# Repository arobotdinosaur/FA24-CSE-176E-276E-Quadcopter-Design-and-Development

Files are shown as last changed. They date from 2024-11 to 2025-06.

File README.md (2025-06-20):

Raw Quadcopters
Quadcopters designed by Kaustubh Kanagalekar and Alexander Haken

## Introduction

In this project class, we were challenged to design a printed circuit board (PCB) quadcopter and program it using Arduino software in order to achieve flight. 

The class was broken into multiple smaller milestones- PCB design for electronic components, PCB design for quadcopter, sensor filtering and calibration, Proportional, Integral, Derivative (PID) tuning, PCB quadcopter assembly, and flight. As we were designing the PCB quadcopter using computer software, we were provided with a test flight control board (FCB) that we could work on concurrently. We could use either the FCB or the custom PCB quadcopter for demonstration purposes. 

The skills that we learned from the class were-
1. PCB design and fabrication
2. Embedded systems programming 
3. Control theory and sensor calibration 

## Electronic Design

Using Fusion 360, we were tasked with designing the following components from scratch- 

1. Resistor (0805 0Ohm) 
2. Red LED 
3. MOSFET (N-channel) 
4. Inertial measurement unit (IMU) (LSM6DSOXTR 6-Axis) 

We referenced the data sheets for each component online and extensively studied the footprints. 
More specifically, we utilised the footprints tab in Fusion 360 to add SMD pads, silkscreens, keepouts, etc. to accurately replicate the dimensions. 

We also took advantage of the automated building tool at times to accurately build the electronic components.  

Footprint of the resistor
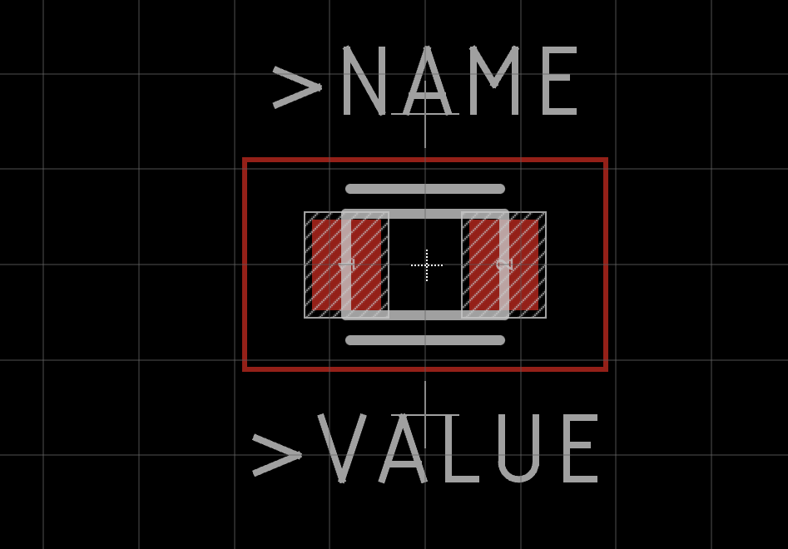
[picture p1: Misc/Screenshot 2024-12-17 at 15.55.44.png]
Footprint of the resistor
 

Footprint of the LED 
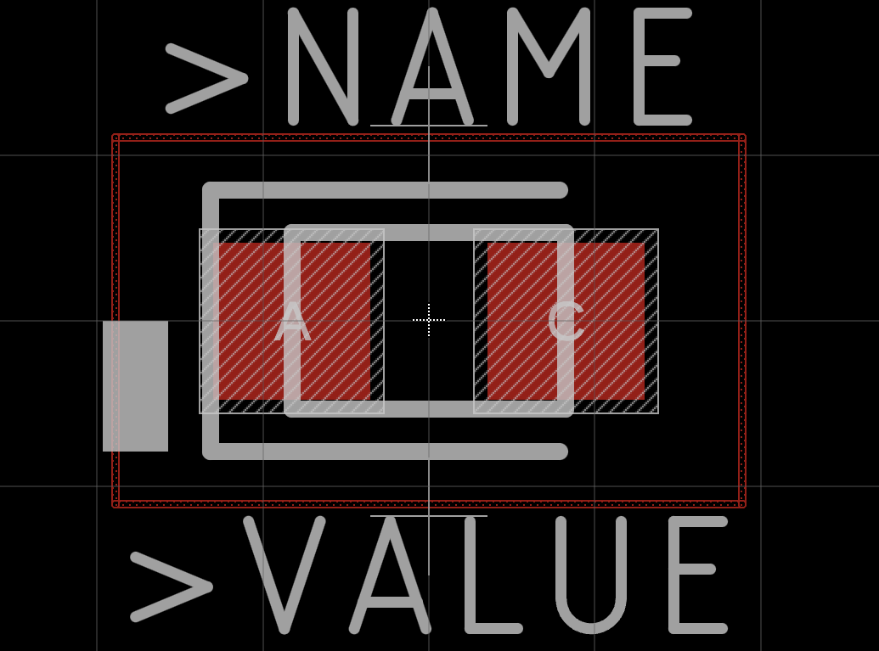
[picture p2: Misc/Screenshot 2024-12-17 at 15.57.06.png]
Footprint of the LED


Footprint of the MOSFET 
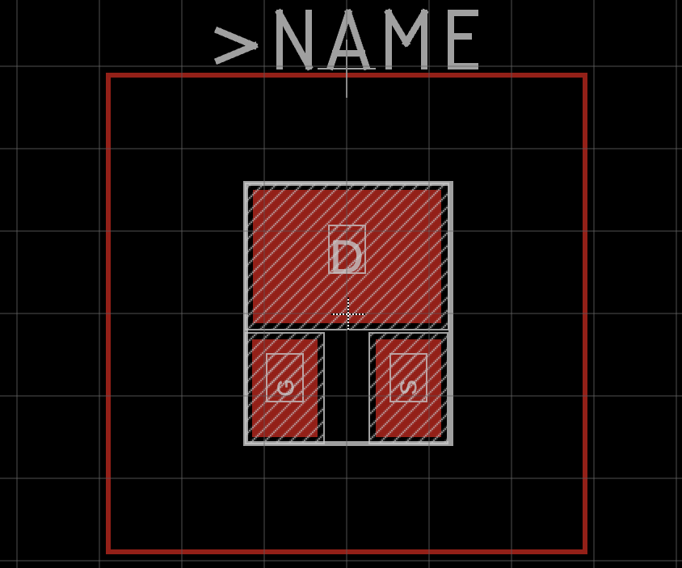
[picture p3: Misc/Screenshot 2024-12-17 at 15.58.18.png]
MOSFET Footprint
 

Footprint of the IMU 
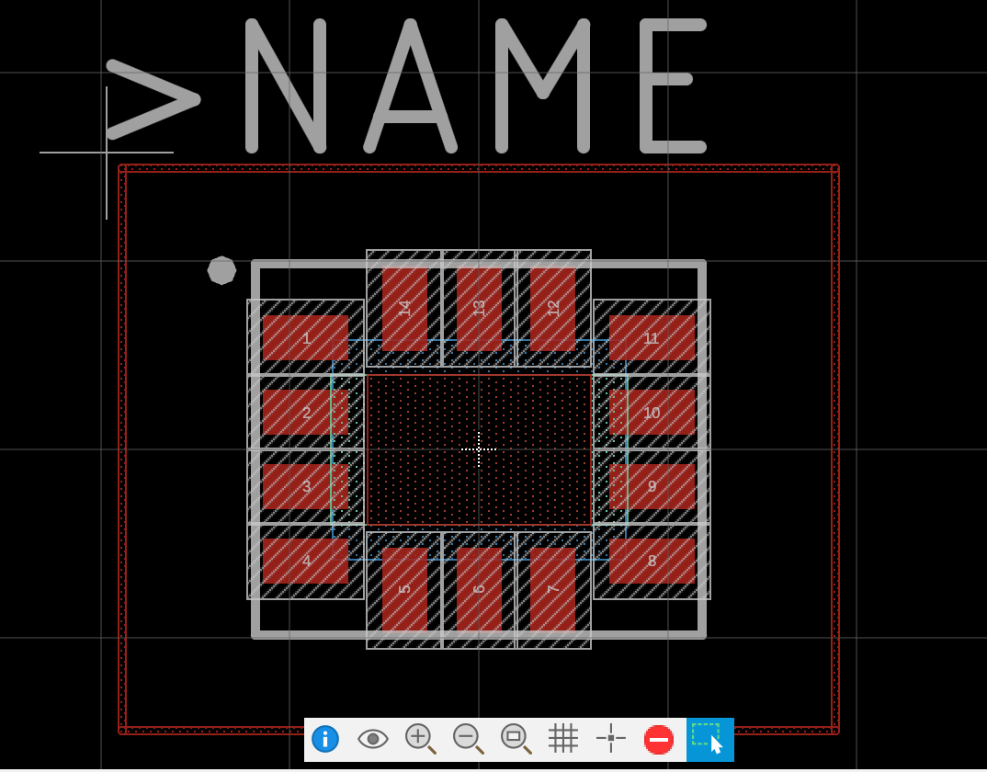
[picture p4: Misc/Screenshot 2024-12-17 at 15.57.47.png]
IMU Footprint


After creating the footprints, we built symbols for each electronic component using the standard IEEE styling conventions using the symbols tab. 

Finally, we connected the footprints and the symbols of each component in the components tab so that we could use them in our quadcopter schematic and design. 

We ensured that we met all the necessary guidelines and requirements set forth by the PCB manufacturer and instructor in our designs.  

## Quadcopter Design 

We were tasked with creating the schematic for the PCB quadcopter. In addition to our custom made components, we were also provided with additional parts from the instructor. 
The quadcopter had multiple smaller sketches- 
1. The microcontroller connections  
2. Bootloader 
3. IMU 
4. Debug/Rescue Header 
5. Motor Driver 
6. Netbridge and power supply 

### Microcontroller connections
We connected various pins and components to the microcontroller. The most significant connection we had was the balun (used for allowing balanced and unbalanced lines to be interfaced without major disturbances in impedances). This was significant as it allowed us to securely connect the antenna in our design. We were deliberate in our antenna placement as incorrect placements would yield spotty data transmission, and the quadcopter may not be able to fly.  

### Bootloader 
The primary objective of including the bootloader was  to load code to the microcontroller. Pins were connected to the microcontroller from the bootloader. 

### IMU 
We established a communication protocol with the microcontroller using I2C (Inter-Integrated Circuit). We incorporated two wires (Serial Data Line and Serial Clock Line) to transmit data between the microcontroller and IMU. 

### Debug/Rescue Header 
The rescue header was incorporated in order to help with debugging signals during testing. We also added a IMU reuse header in case our soldered IMU had issues. 

### Motor Driver 
We built four copies of the motor driver sketch as there were four motors driving the quadcopter. We included motor pads, mosfets, and a diode in the sketch. More importantly, we also included a decoupling capacitor to help absorb switching noise from the motors.

### Netbridge and Power Supply 
We designed a low-dropout voltage regulator in the schematic to provide a stable power output of 3V to the motors. This was because the batteries were providing power ranging from 4V to 5V. We had two power rails: An unregulated power rail (called VBAT) that provides power to the motors and input of the voltage regulator and is driven directly by the battery, and a regulated supply driven by the voltage regulator (called 3V) 

A netbridge was also created in order to electrically connect two nets in a schematic while keeping the nets separate in schematic . This was done to connect digital ground (BAT_GND) to regular ground. 

Image of the overall schematic 
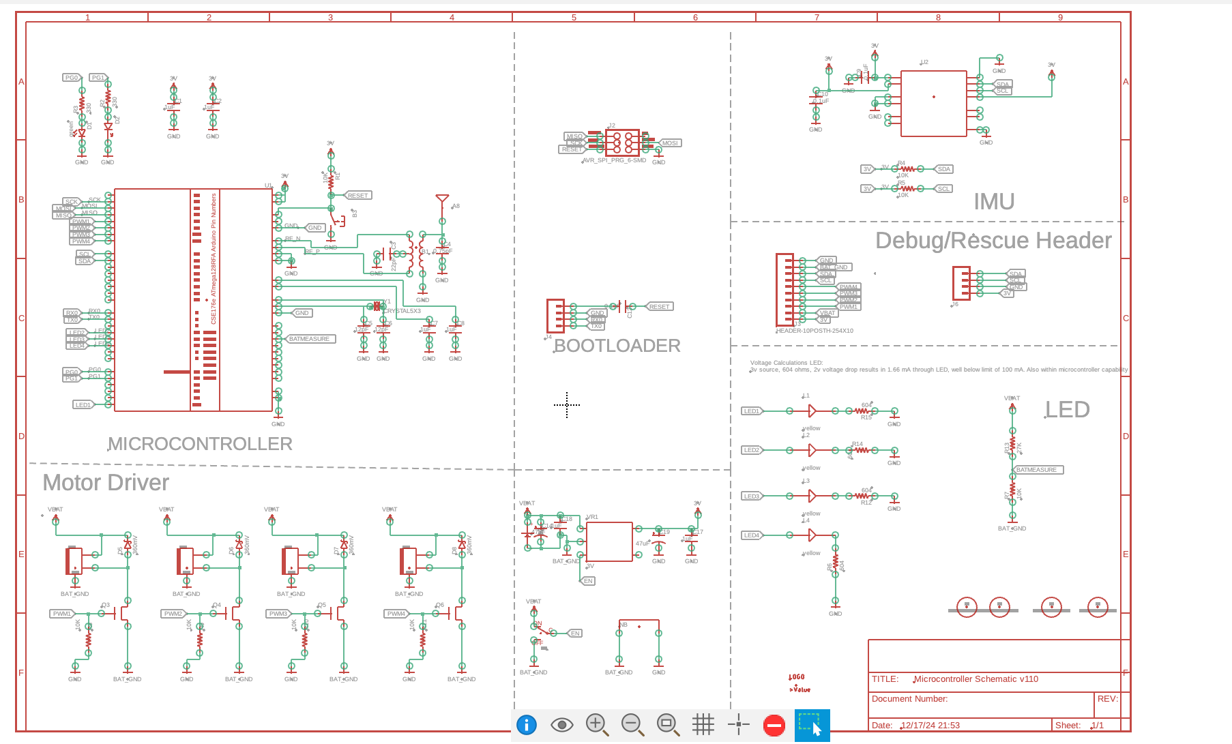
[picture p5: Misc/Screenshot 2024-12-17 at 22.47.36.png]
Schematic


### PCB Design 
We created a custom shape for the quadcopter and placed all the necessary components from the sketch to the board. The placement of some components were extremely important- for example, the antenna had to be placed near the edge of the board for uninterrupted communication, and the IMU had to be placed at the centre for accurate measurements. The crystal was placed close to the microcontroller, and the motor controllers were placed at the edges of the board. 

We primarily used the autorouter to route all wirings and connections, except in the case of the antenna and parts of the microcontroller. The antenna had to be connected with a large wire (50 mm) manually to the balun and other components (such as the corresponding  microcontroller pins and capacitors). The crystal also had to manually routed with specific pins of the microcontroller. We utilized differential pairs for sending the signals from the antenna and crystal back to the microcontroller due to the sensitivity of these components.

The board had to fit under a 13.9 cm square requirement  with motor holes of 12.2 mm for optimal placement. 
In Fusion 360, the board was aligned to a 1 mm grid for aesthetic reasons. 

We had four layers on the board in order to manage all the wirings and connections succinctly. We had a top layer, bottom layer, and two internal layers (one for 3V/VBAT and the other for GND/BAT_GND). The top and bottom layers involved signal routing for connecting various electronic components. The bottom plan was used whenever possible to reduce electrical noise. The 3V/VBAT and GND/BAT_GND layers were exclusively used for delivering power and ground signals, respectively. The traces that carried both power and ground signals were as short as possible to provide a low-resistance path for current to flow. 
We took care to leave a gap in all the layers beneath the IMU as the manufacture specified that we should not have metal underneath it for best performance.
 
Image of the connected boards in Fusion 360.
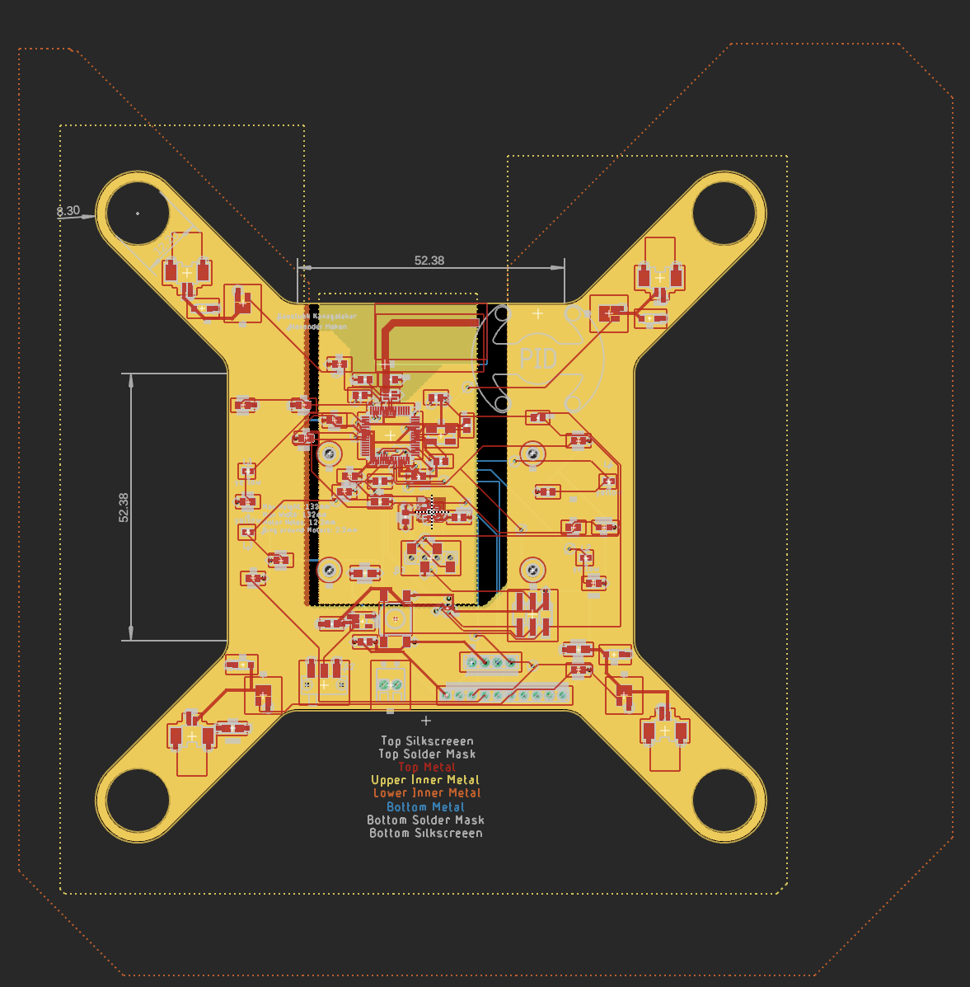
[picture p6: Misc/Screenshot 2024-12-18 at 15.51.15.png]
Board 1

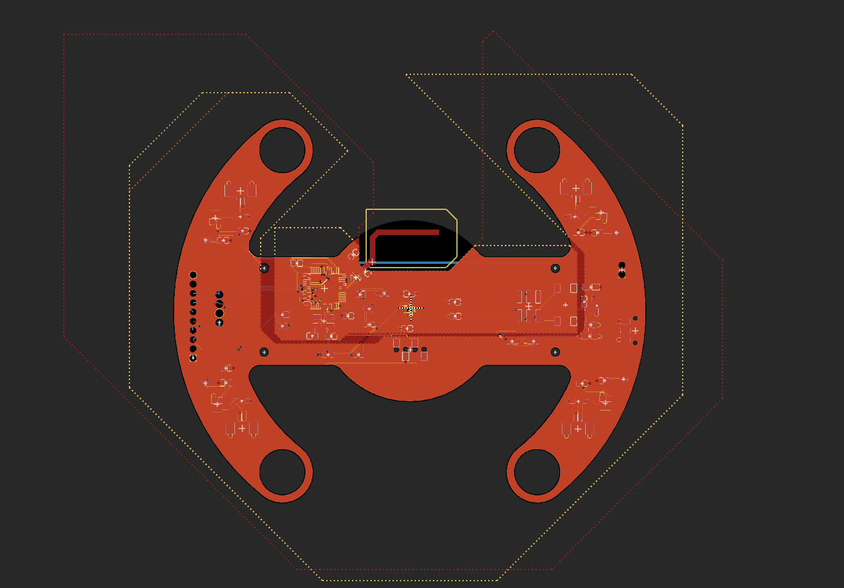
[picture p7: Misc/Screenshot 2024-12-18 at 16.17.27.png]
Board 2


## Sensor Filtering and Calibration 

Prior to reading data from the IMU, we had to establish a connection between a test remote and the FCB; we accomplished this using a check-sum that would transmit data sent from the remote (such as throttle value, pitch, roll, yaw) to the FCB. In addition, we also wrote code that read the existing gimbal value from the remote and transmitted it to the FCB to achieve flight. 
The check-sum was created in order to prevent bad data packets from getting sent over and to only accept packets that were sent from our remote (and not from other groups). 

On the FCB, we had to read data from the IMU to accurately measure the orientation. We used an existing library corresponding to the IMU called Adafruit_AHRS- from this, we used the `Adafruit_Simple_AHRS::getQuadOrientation()` function to gather all the necessary data.
We obtained the pitch rate, roll, and yaw from the quad orientation function.  
After gathering these data from the IMU, we created a complementary filter to filter out some of the noise created by the accelerometer and gyroscope. The accelerometer (Euler angles of the orientation) and gyroscope readings (the angular accelerations) were taken from the IMU. 
The reason we created a complementary filter was to gather the best possible data from both the gyroscope and the accelerometer as each inertial sensor has positives and drawbacks. The accelerometers do not drift over time, but they are quite noisy when the motors are running, and slightly less responsive compared to the gyroscope. Whereas, gyroscopes are less noisy than  the accelerometers, but the resulting measurement will drift over time due to accumulated error. We tried to set a high gain such that we could extract more data from the gyroscope in our code. 
We used a standard formula shown below with a gain of 0.98- `cf_angle = (gain) * (cf_angle + (gyro_raw * RAD_TO_DEG * dt)) + (1-gain) * (acc_angle)`

`RAD_TO_DEG = 57.295779513082320876798154814105`
`cf_angle` is the angle resulted from the complementary  filter, `gyro_raw` is the gyroscope measurement, `acc_angle` is the Euler angles, `dt` is the change in time from the measurements.  

We also accounted for any offsets caused by the IMU in the code to have it read zero when levelled. 
We only performed complementary filtering on the roll and pitch axes. 

## PID Control and Tuning 
PID is a type of controller used in feedback systems to regulate speed, position, and various other parameters to ensure stability. We used PID to keep the FCB stable and levelled when the motors were running. 
Proportional (P) responds to the current error and provides immediate action 
Integral (I) accumulates past errors 
Derivative (D) predicts future errors based on the rate of change. 
This was implemented for the pitch and roll axes using the following equation- 
`PID = (Kp* error) + Ki* integral - Kd* derivative` 
Where `Kp, Ki, Kd` are constants that are determined by testing, `error` is the difference from the remote gimbal input and the offset of the axis (`error = setpoint - corrected`), `integral` is `integral = error* dt+integral` , and derivative is the raw gyro readings in degrees. We used the raw gyro readings rather than doing a numerical derivative of cf_pitch because the raw gyroscope readings had slightly less delay. 

PID for yaw rate was implemented a bit differently. The control was only proportional to on the velocity error in yaw, which we got directly from the raw gyroscope yaw data.

After writing the code for all three axes control, we combined them so that there would be an equal output to the motors. We implemented a mixing function which increased the power for the front motors and decreased the power for the rear motors based on the PID output.

Through trial and error, we were able to find the optimal `Kp, Ki, Kd` values for the various axes to achieve stability. For pitch and roll: a ‘P’ overshoot would have resulted in the FCB “sway” from one end to another, an ‘I’ overshoot would have resulted in levelling at an odd angle, and a ‘D’ overshoot would have resulted in the FCB oscillating rapidly. Undershoots of each would have resulted in the quad not being able to move at all. For yaw rate, overshoots of ‘P’ and ‘D’ resulted in the FCB spinning uncontrollably in space, whereas undershoots would have not caused any motion. 

One critical factor for having reliable PID control was having a fast control loop running on the microcontroller. We initially had issues with "derivative kick" where the derivative term was causing unstable behavior due to a high control latency. To optimize speed, we made sure that only critical processes were running. Once we commented out all the print statements that we'd been using for debugging, the loop time reduced from about 35 ms to only 8 ms, and our PID controller ran much better.

For determining the yaw rate coefficients, our control was proportional to the yaw rate error (thus we did not have a `Kd` value after testing).  

This is a video of the PID demonstration for the pitch axis
PID Demo video

## PCB Assembly 
After our PCB quadcopter boards were manufactured, we started on the assembly portion of the board. We applied solder paste to our boards using a stencil (a thin aluminium sheet with precise holes corresponding to the board). Immediately after, we attached all the necessary electronic components by hand, ensuring accuracy and precision. We later used a reflow oven to connect the components and the PCB pads as a reflow oven guarantees a secure connections between the paste applied to the PCB pads and the attached components. 
 
Picture of assembly after reflow (note that some components were missing due to unavailability at the time of assembly) 
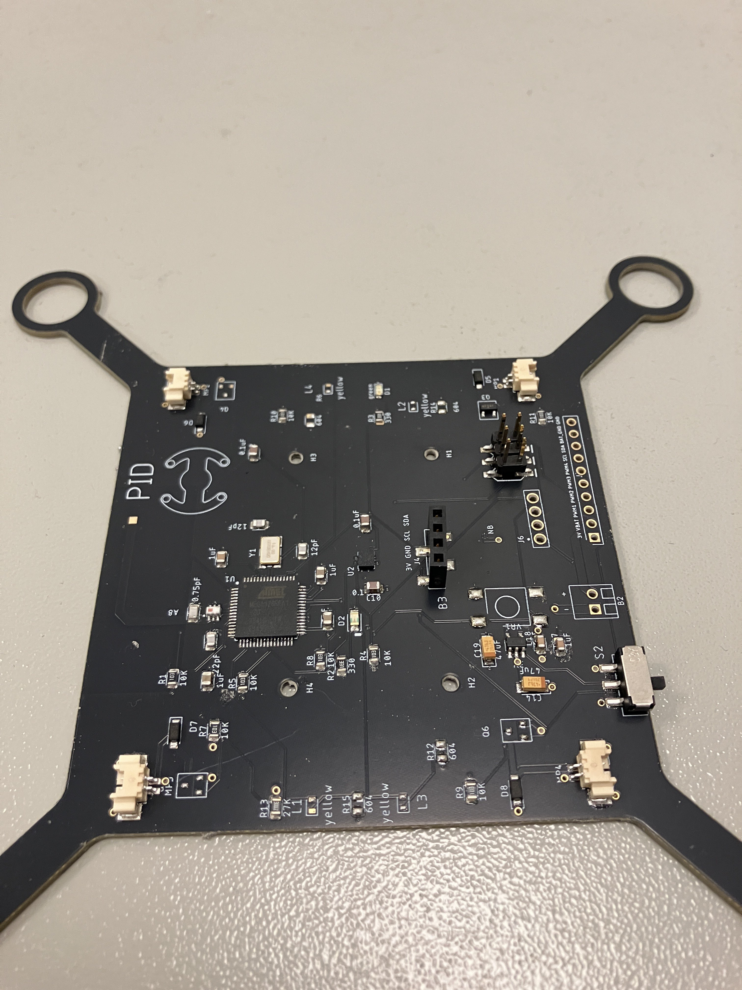
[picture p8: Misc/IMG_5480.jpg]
Incomplete Assembly


## Flight 
We demonstrated flight using the provided FCB. 

Flight was broken into the following categories- 
1. "Roombaing" -- moving around the the floor with dowels installed with direction control and minimal yaw
2. Repeated, vertical hopping (>1 inches, > 0.25 second)
3. Repeated, vertical hopping (>6 inches, > 1 second)
4. Repeated, vertical hopping (>12 inches, > 3 seconds)
5. Short flight (>12 inches, > 6 seconds)
6. Sustained flight (> 12 inches, > 10 seconds, demonstrate yaw control)
7. 	Sustained flight (Fly long enough to consume an entire battery)

In this phase, we had also implemented a “trimming” mechanism where we would manually offset any discrepancies in pitch and roll to ensure a level flight takeoff. We would test which direction the FCB would travel towards when throttle was applied and would adjust any errors according. Trimming would have to be done every time we flew from a different location as ground would be levelled differently at each location. 

In our final demonstration, we were able to achieve FL 5. 

Please download the video after clicking the "?" icon to view the flight
Flight video

## Acknowledgements
We would like to thank our instructor, Dr. Steven Swanson, our TA, Zifeng Zhang, and our classmates for their assistance and guidance with the project.  
Here is the [link](https://github.com/NVSL/QuadClass-Resources) to the main quadcopter class repository.

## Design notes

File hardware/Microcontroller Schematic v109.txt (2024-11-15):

Partl	ist exported from /var/folders/44/drcq5kgn0vjf1mzfb_	9lj2d80000gn/T/Neutron/ElectronFileOutput/3953/sch-0	e0f0b5e-81eb-4e8a-b25f-d82639070f14	/Microcontroller Schematic v109.sch at 11/14/24 11:19 AM												
																
Part	Value	Device	Package	Description	CREATOR             CUSTOM DATASHEET	DESC	DIST	DISTPN	MFR	MOUNTING	MPN	PACKAGE PIN1 PIN2 POPULATE PRICE PROD_ID	REVIEWER	VALUE		Done
A8	ANTENNA-BOARD	ANTENNA-BOARD	ANT_PCB_2.4GHZ_NRF8001_1.6MM_1OZ	Single endded antenna.	Swanson	trace antenna	NA	NA	NA	NONE	NA	NO				n/a
B1	BALUN0805	BALUN0805	BALUN	A balun to convert differential radio-frequency outputs from the microcontroller into a single-ended driver for the antenna.	Swanson                    http://katalog.we-online.de/pbs/datasheet/748421245.pdf	BALUN 2.4GHZ-2.5GHZ 50/100 0805	Digikey	732-2230-1-ND	Wurth Electronics Inc.	SMD	748421245	0805                       2.63	Swanson			yes
B2	BATTERY-SCREW-TERMINAL	BATTERY-SCREW-TERMINAL	SCREW-TERMINAL-1X2-2.54MM	Connections for a battery.	Swanson		DIGIKEY	ED10561-ND		TH		-    +				yes
B3	PUSHBUTTON_SMD-VERTICAL-1	PUSHBUTTON_SMD-VERTICAL-1	TE_FSM8JSMA_HS	"""Tactile"" or ""clicky"" button."	Swanson		Digikey	450-1129-ND	TE Connectivity Alcoswitch Switches	SMD	FSM4JSMA		Swanson			yes
C1	1uF	CAPACITOR-NP_SMD-2012-0805_CERAMIC-1UF	CAPC2012X140_HS	Nonpolarized capacitor	Swanson		Digikey	587-1281-1-ND	Taiyo Yuden	SMD	TMK212B7105KG-T		Swanson	1uF		yes
C2	1uF	CAPACITOR-NP_SMD-2012-0805_CERAMIC-1UF	CAPC2012X140_HS	Nonpolarized capacitor	Swanson		Digikey	587-1281-1-ND	Taiyo Yuden	SMD	TMK212B7105KG-T		Swanson	1uF		yes
C3	22pF	CAPACITOR-NP_SMD-2012-0805_CERAMIC-22PF	CAPC2012X140_HS	Nonpolarized capacitor	Swanson	CAP CER 22PF 250V C0G/NP0 0805	Digikey	490-5534-1-ND	Murata Electronics	SMD	GRM21A5C2E220JW01D	0805	Swanson	22pF		yes
C4	0.75pF	CAPACITOR-NP_SMD-2012-0805_CERAMIC-0.75PF	CAPC2012X140_HS	Nonpolarized capacitor	Swanson	CAP CER 0.75PF 100V C0G/NP0 0805	Digikey	490-3585-1-ND	Murata Electronics	SMD	GQM2195C2AR75CB01D	0805	Swanson	0.75pF		yes
C5	12pF	CAPACITOR-NP_SMD-2012-0805_CERAMIC-12PF	CAPC2012X140_HS	Nonpolarized capacitor	Swanson	CAP CER 12PF 250V C0G/NP0 0805	Digikey	490-5531-1-ND	Murata Electronics	SMD	GRM21A5C2E120JW01D	0805	Swanson	12pF		yes
C6	12pF	CAPACITOR-NP_SMD-2012-0805_CERAMIC-12PF	CAPC2012X140_HS	Nonpolarized capacitor	Swanson	CAP CER 12PF 250V C0G/NP0 0805	Digikey	490-5531-1-ND	Murata Electronics	SMD	GRM21A5C2E120JW01D	0805	Swanson	12pF		yes
C7	1uF	CAPACITOR-NP_SMD-2012-0805_CERAMIC-1UF	CAPC2012X140_HS	Nonpolarized capacitor	Swanson		Digikey	587-1281-1-ND	Taiyo Yuden	SMD	TMK212B7105KG-T		Swanson	1uF		yes
C8	1uF	CAPACITOR-NP_SMD-2012-0805_CERAMIC-1UF	CAPC2012X140_HS	Nonpolarized capacitor	Swanson		Digikey	587-1281-1-ND	Taiyo Yuden	SMD	TMK212B7105KG-T		Swanson	1uF		yes
C9	0.1uF	CAPACITOR-NP_SMD-2012-0805_CERAMIC-0.1UF	CAPC2012X140_HS	Nonpolarized capacitor	Swanson	CAP CER 0.1UF 100V X7R 0805	Digikey	445-1418-1-ND	TDK Corporation	SMD	C2012X7R2A104K125AA	0805	Swanson	0.1uF		yes
C10	0.1uF	CAPACITOR-NP_SMD-2012-0805_CERAMIC-0.1UF	CAPC2012X140_HS	Nonpolarized capacitor	Swanson	CAP CER 0.1UF 100V X7R 0805	Digikey	445-1418-1-ND	TDK Corporation	SMD	C2012X7R2A104K125AA	0805	Swanson	0.1uF		yes
C12	0.1uF	CAPACITOR-NP_SMD-2012-0805_CERAMIC-0.1UF	CAPC2012X140_HS	Nonpolarized capacitor	Swanson	CAP CER 0.1UF 100V X7R 0805	Digikey	445-1418-1-ND	TDK Corporation	SMD	C2012X7R2A104K125AA	0805	Swanson	0.1uF		yes
C14	47uF	CAPACITOR-POL_47UF-SMD-1206-TAJA	CAPMP3216X180	Polarized capacitor	Swanson	CAP TANT 47UF 10% 6.3V 1206	DIGIKEY	478-11462-1-ND	AVX Corporation	SMD	TAJA476K006SNJV	1206		47uF		yes
C17	1uF	CAPACITOR-NP_SMD-2012-0805_CERAMIC-1UF	CAPC2012X140_HS	Nonpolarized capacitor	Swanson		Digikey	587-1281-1-ND	Taiyo Yuden	SMD	TMK212B7105KG-T		Swanson	1uF		yes
C18	1uF	CAPACITOR-NP_SMD-2012-0805_CERAMIC-1UF	CAPC2012X140_HS	Nonpolarized capacitor	Swanson		Digikey	587-1281-1-ND	Taiyo Yuden	SMD	TMK212B7105KG-T		Swanson	1uF		yes
C19	47uF	CAPACITOR-POL_47UF-SMD-1206-TAJA	CAPMP3216X180	Polarized capacitor	Swanson	CAP TANT 47UF 10% 6.3V 1206	DIGIKEY	478-11462-1-ND	AVX Corporation	SMD	TAJA476K006SNJV	1206		47uF		yes
D1	green	DIODE-LED_SMD-2012-0805-GREEN	LEDSC125X200X120-2_HS	Light emitting diode	Swanson		Digikey	160-1179-1-ND	Lite-On Inc	SMD	LTST-C170GKT		Swanson	green		yes
D2		LED-RED-160-1178-1-ND	LED_160-1178-1-ND		KaustubhKanagalekar		Digikey	160-1178-1-ND								yes
D5	360mV	DIODE-SCHOTTKY_-SMD-SOD123	SODFL3516X96	Schottky diode	Swanson	DIODE SCHOTTKY 30V 1.5A SFLAT	Digikey	CRS08QMCT-ND	Toshiba Semiconductor and Storage	SMD	"CRS08(TE85L,Q,M)"		Swanson	360mV		yes
D6	360mV	DIODE-SCHOTTKY_-SMD-SOD123	SODFL3516X96	Schottky diode	Swanson	DIODE SCHOTTKY 30V 1.5A SFLAT	Digikey	CRS08QMCT-ND	Toshiba Semiconductor and Storage	SMD	"CRS08(TE85L,Q,M)"		Swanson	360mV		yes
D7	360mV	DIODE-SCHOTTKY_-SMD-SOD123	SODFL3516X96	Schottky diode	Swanson	DIODE SCHOTTKY 30V 1.5A SFLAT	Digikey	CRS08QMCT-ND	Toshiba Semiconductor and Storage	SMD	"CRS08(TE85L,Q,M)"		Swanson	360mV		yes
D8	360mV	DIODE-SCHOTTKY_-SMD-SOD123	SODFL3516X96	Schottky diode	Swanson	DIODE SCHOTTKY 30V 1.5A SFLAT	Digikey	CRS08QMCT-ND	Toshiba Semiconductor and Storage	SMD	"CRS08(TE85L,Q,M)"		Swanson	360mV		yes
H1	MOUNTING_HOLE-2-56	MOUNTING_HOLE-2-56	2-56-MOUNTING-HOLE-NO-METAL													n/a
H2	MOUNTING_HOLE-2-56	MOUNTING_HOLE-2-56	2-56-MOUNTING-HOLE-NO-METAL													n/a
H3	MOUNTING_HOLE-2-56	MOUNTING_HOLE-2-56	2-56-MOUNTING-HOLE-NO-METAL													n/a
H4	MOUNTING_HOLE-2-56	MOUNTING_HOLE-2-56	2-56-MOUNTING-HOLE-NO-METAL													n/a
J2	AVR_SPI_PRG_6-SMD	AVR_SPI_PRG_6-SMD	2X3-SMD	AVR ISP 6 Pin	Swanson	CONN HEADER SMD 6POS 2.54MM	Digikey	609-3487-2-ND	Amphenol ICC (FCI)	SMD	95278-101A06LF					yes
J3	HEADER-10POSTH-254X10	HEADER-10POSTH-254X10	HDRV10W63P254_10X1_2540X254H838_HS	"10 pin single inline pin header, socket, or connector"	Swanson                    http://portal.fciconnect.com/Comergent//fci/drawing/68000.pdf		Digikey	609-3250-ND	Amphenol FCI	TH	68000-110HLF	0.55	Swanson			yes
J4	HEADER-4POS-0.1IN-FEMALE-SMD-BOTTOM-ENTRY	HEADER-4POS-0.1IN-FEMALE-SMD-BOTTOM-ENTRY	HEADER-1X4-BOTTOM-ENTRY		Swanson	CONN RCPT 4POS 0.1 GOLD SMD	DIGIKEY	A121787CT-ND	TE Connectivity AMP Connectors	SMD	1241152-4					no I think out
J6	HEADER-4POS-0.1IN-FEMALE	HEADER-4POS-0.1IN-FEMALE	HDRVR4W80P254_1X4_1066X254X850B		Swanson		Digikey	S7002-ND								yes
L1	yellow	LED_YELLOW	LEDC1507X80NYELLOW		AlexanderHaken      CUSTOM		Digikey	150060YS75000								
L2	yellow	LED_YELLOW	LEDC1507X80NYELLOW		AlexanderHaken      CUSTOM		Digikey	150060YS75000								
L3	yellow	LED_YELLOW	LEDC1507X80NYELLOW		AlexanderHaken      CUSTOM		Digikey	150060YS75000								
L4	yellow	LED_YELLOW	LEDC1507X80NYELLOW		AlexanderHaken      CUSTOM		Digikey	150060YS75000								
LOGO	PIDLOGO	PIDLOGO	PIDLOGO													n/a
MP1	MOTOR_PADS_GND-MOLEX-SMD	MOTOR_PADS_GND-MOLEX-SMD	MOLEX-0532610271	Connections a brushed motor.	Swanson	CONN HEADER SMD R/A 2POS 1.25MM	DIGIKEY	WM7620CT-ND	Molex	SMD	532610271					yes
MP2	MOTOR_PADS_GND-MOLEX-SMD	MOTOR_PADS_GND-MOLEX-SMD	MOLEX-0532610271	Connections a brushed motor.	Swanson	CONN HEADER SMD R/A 2POS 1.25MM	DIGIKEY	WM7620CT-ND	Molex	SMD	532610271					yes
MP3	MOTOR_PADS_GND-MOLEX-SMD	MOTOR_PADS_GND-MOLEX-SMD	MOLEX-0532610271	Connections a brushed motor.	Swanson	CONN HEADER SMD R/A 2POS 1.25MM	DIGIKEY	WM7620CT-ND	Molex	SMD	532610271					yes
MP4	MOTOR_PADS_GND-MOLEX-SMD	MOTOR_PADS_GND-MOLEX-SMD	MOLEX-0532610271	Connections a brushed motor.	Swanson	CONN HEADER SMD R/A 2POS 1.25MM	DIGIKEY	WM7620CT-ND	Molex	SMD	532610271					yes
NB	NETBRIDGE	NETBRIDGE	NETBRIDGE													n/a
Q3	MOSFET-FET-SI2302CDS-T1-E3CT-NDSI2302CDS-T1-E3CT-ND	MOSFET-FET-SI2302CDS-T1-E3CT-NDSI2302CDS-T1-E3CT-ND	MOSFET_FET_SI2302CDS-T1-E3CT-ND		KaustubhKanagalekar		Digikey	SI2302CDS-T1-E3CT-ND								yes
Q4	MOSFET-FET-SI2302CDS-T1-E3CT-NDSI2302CDS-T1-E3CT-ND	MOSFET-FET-SI2302CDS-T1-E3CT-NDSI2302CDS-T1-E3CT-ND	MOSFET_FET_SI2302CDS-T1-E3CT-ND		KaustubhKanagalekar		Digikey	SI2302CDS-T1-E3CT-ND								yes
Q5	MOSFET-FET-SI2302CDS-T1-E3CT-NDSI2302CDS-T1-E3CT-ND	MOSFET-FET-SI2302CDS-T1-E3CT-NDSI2302CDS-T1-E3CT-ND	MOSFET_FET_SI2302CDS-T1-E3CT-ND		KaustubhKanagalekar		Digikey	SI2302CDS-T1-E3CT-ND								yes
Q6	MOSFET-FET-SI2302CDS-T1-E3CT-NDSI2302CDS-T1-E3CT-ND	MOSFET-FET-SI2302CDS-T1-E3CT-NDSI2302CDS-T1-E3CT-ND	MOSFET_FET_SI2302CDS-T1-E3CT-ND		KaustubhKanagalekar		Digikey	SI2302CDS-T1-E3CT-ND								yes
R1	10K	RESISTOR_SMD-2012-0805-10K	RESC2012X60_HS	Resistor	Swanson	RES SMD 10K OHM 5% 1/8W 0805	Digikey	311-10KARCT-ND	Yageo	SMD	RC0805JR-0710KL	0805	Swanson	10K		yes
R2	330	RESISTOR_SMD-2012-0805-330	RESC2012X60_HS	Resistor	Swanson		Digikey	311-330ARCT-ND	Yageo	SMD	RC0805JR-07330RL		Swanson	330		yes
R3	330	RESISTOR_SMD-2012-0805-330	RESC2012X60_HS	Resistor	Swanson		Digikey	311-330ARCT-ND	Yageo	SMD	RC0805JR-07330RL		Swanson	330		yes
R4	10K	RESISTOR_SMD-2012-0805-10K	RESC2012X60_HS	Resistor	Swanson	RES SMD 10K OHM 5% 1/8W 0805	Digikey	311-10KARCT-ND	Yageo	SMD	RC0805JR-0710KL	0805	Swanson	10K		yes
R5	10K	RESISTOR_SMD-2012-0805-10K	RESC2012X60_HS	Resistor	Swanson	RES SMD 10K OHM 5% 1/8W 0805	Digikey	311-10KARCT-ND	Yageo	SMD	RC0805JR-0710KL	0805	Swanson	10K		yes
R6	604	RESISTOR_SMD-2012-0805-604	RESC2012X60_HS	Resistor	Swanson		DIGIKEY	311-604CRCT-ND		SMD				604		
R7	10K	RESISTOR_SMD-2012-0805-10K	RESC2012X60_HS	Resistor	Swanson	RES SMD 10K OHM 5% 1/8W 0805	Digikey	311-10KARCT-ND	Yageo	SMD	RC0805JR-0710KL	0805	Swanson	10K		yes
R8	10K	RESISTOR_SMD-2012-0805-10K	RESC2012X60_HS	Resistor	Swanson	RES SMD 10K OHM 5% 1/8W 0805	Digikey	311-10KARCT-ND	Yageo	SMD	RC0805JR-0710KL	0805	Swanson	10K		yes
R9	10K	RESISTOR_SMD-2012-0805-10K	RESC2012X60_HS	Resistor	Swanson	RES SMD 10K OHM 5% 1/8W 0805	Digikey	311-10KARCT-ND	Yageo	SMD	RC0805JR-0710KL	0805	Swanson	10K		yes
R10	10K	RESISTOR_SMD-2012-0805-10K	RESC2012X60_HS	Resistor	Swanson	RES SMD 10K OHM 5% 1/8W 0805	Digikey	311-10KARCT-ND	Yageo	SMD	RC0805JR-0710KL	0805	Swanson	10K		yes
R11	10K	RESISTOR_SMD-2012-0805-10K	RESC2012X60_HS	Resistor	Swanson	RES SMD 10K OHM 5% 1/8W 0805	Digikey	311-10KARCT-ND	Yageo	SMD	RC0805JR-0710KL	0805	Swanson	10K		yes
R12	604	RESISTOR_SMD-2012-0805-604	RESC2012X60_HS	Resistor	Swanson		DIGIKEY	311-604CRCT-ND		SMD				604		
R13	27K	RESISTOR_SMD-2012-0805-27K	RESC2012X60_HS	Resistor	Swanson		DIGIKEY	311-27.0KCRCT-ND		SMD				27K		got 30k instead for now
R14	604	RESISTOR_SMD-2012-0805-604	RESC2012X60_HS	Resistor	Swanson		DIGIKEY	311-604CRCT-ND		SMD				604		
R15	604	RESISTOR_SMD-2012-0805-604	RESC2012X60_HS	Resistor	Swanson		DIGIKEY	311-604CRCT-ND		SMD				604		
S2	POWER-SWITCH-MFS201N-9-Z-SMD-EDGE	POWER-SWITCH-MFS201N-9-Z-SMD-EDGE	JS102011SAQN		Swanson	SWITCH SLIDE SPDT 300MA 6V	DIGIKEY	401-1999-1-ND	C&K	SMD	JS102011SAQN					yes
U1	ATMEGA128RFA1	ATMEGA128RFA1	QFN-64	ATmega128RFA1	Swanson                    http://www.atmel.com/Images/Atmel-8266-MCU_Wireless-ATmega128RFA1_Datasheet.pdf	IC RF TXRX+MCU 802.15.4 64VFQFN	Digikey	ATMEGA128RFA1-ZU-ND	Microchip Technology	SMD	ATMEGA128RFA1-ZU	QFN                        10.21	Swanson			yes
U2	IMU-LSM6DSOXTR-497-18367-1-ND497-18367-1-ND	IMU-LSM6DSOXTR-497-18367-1-ND497-18367-1-ND	LSM6DS0		KaustubhKanagalekar		Digikey	497-18367-1-ND								yes
VR1	3V	TPS73633-DBVT3V	SOT23-DBV	LP3985-series voltage regulators.	Swanson                    http://www.ti.com/lit/ds/symlink/lp3985.pdf		Digikey	LP3985IM5X-3.0/NOPBCT-ND	Texas Instruments	SMD	LP3985IM5X-3.0/NOPB	0.59	Swanson	3V		yes
Y1	CRYSTAL5X3	CRYSTAL5X3	CRYSTAL-SMD-5X3	"Crystals to provide clock references for microcontrollers, etc."	Swanson                    http://www.abracon.com/Resonators/abm3b.pdf	CRYSTAL 16.0000MHZ 18PF SMD	Digikey	535-9122-1-ND	Abracon LLC	SMD	ABM3B-16.000MHZ-B2-	T                            0.68  XTAL-08218	Swanson			yes

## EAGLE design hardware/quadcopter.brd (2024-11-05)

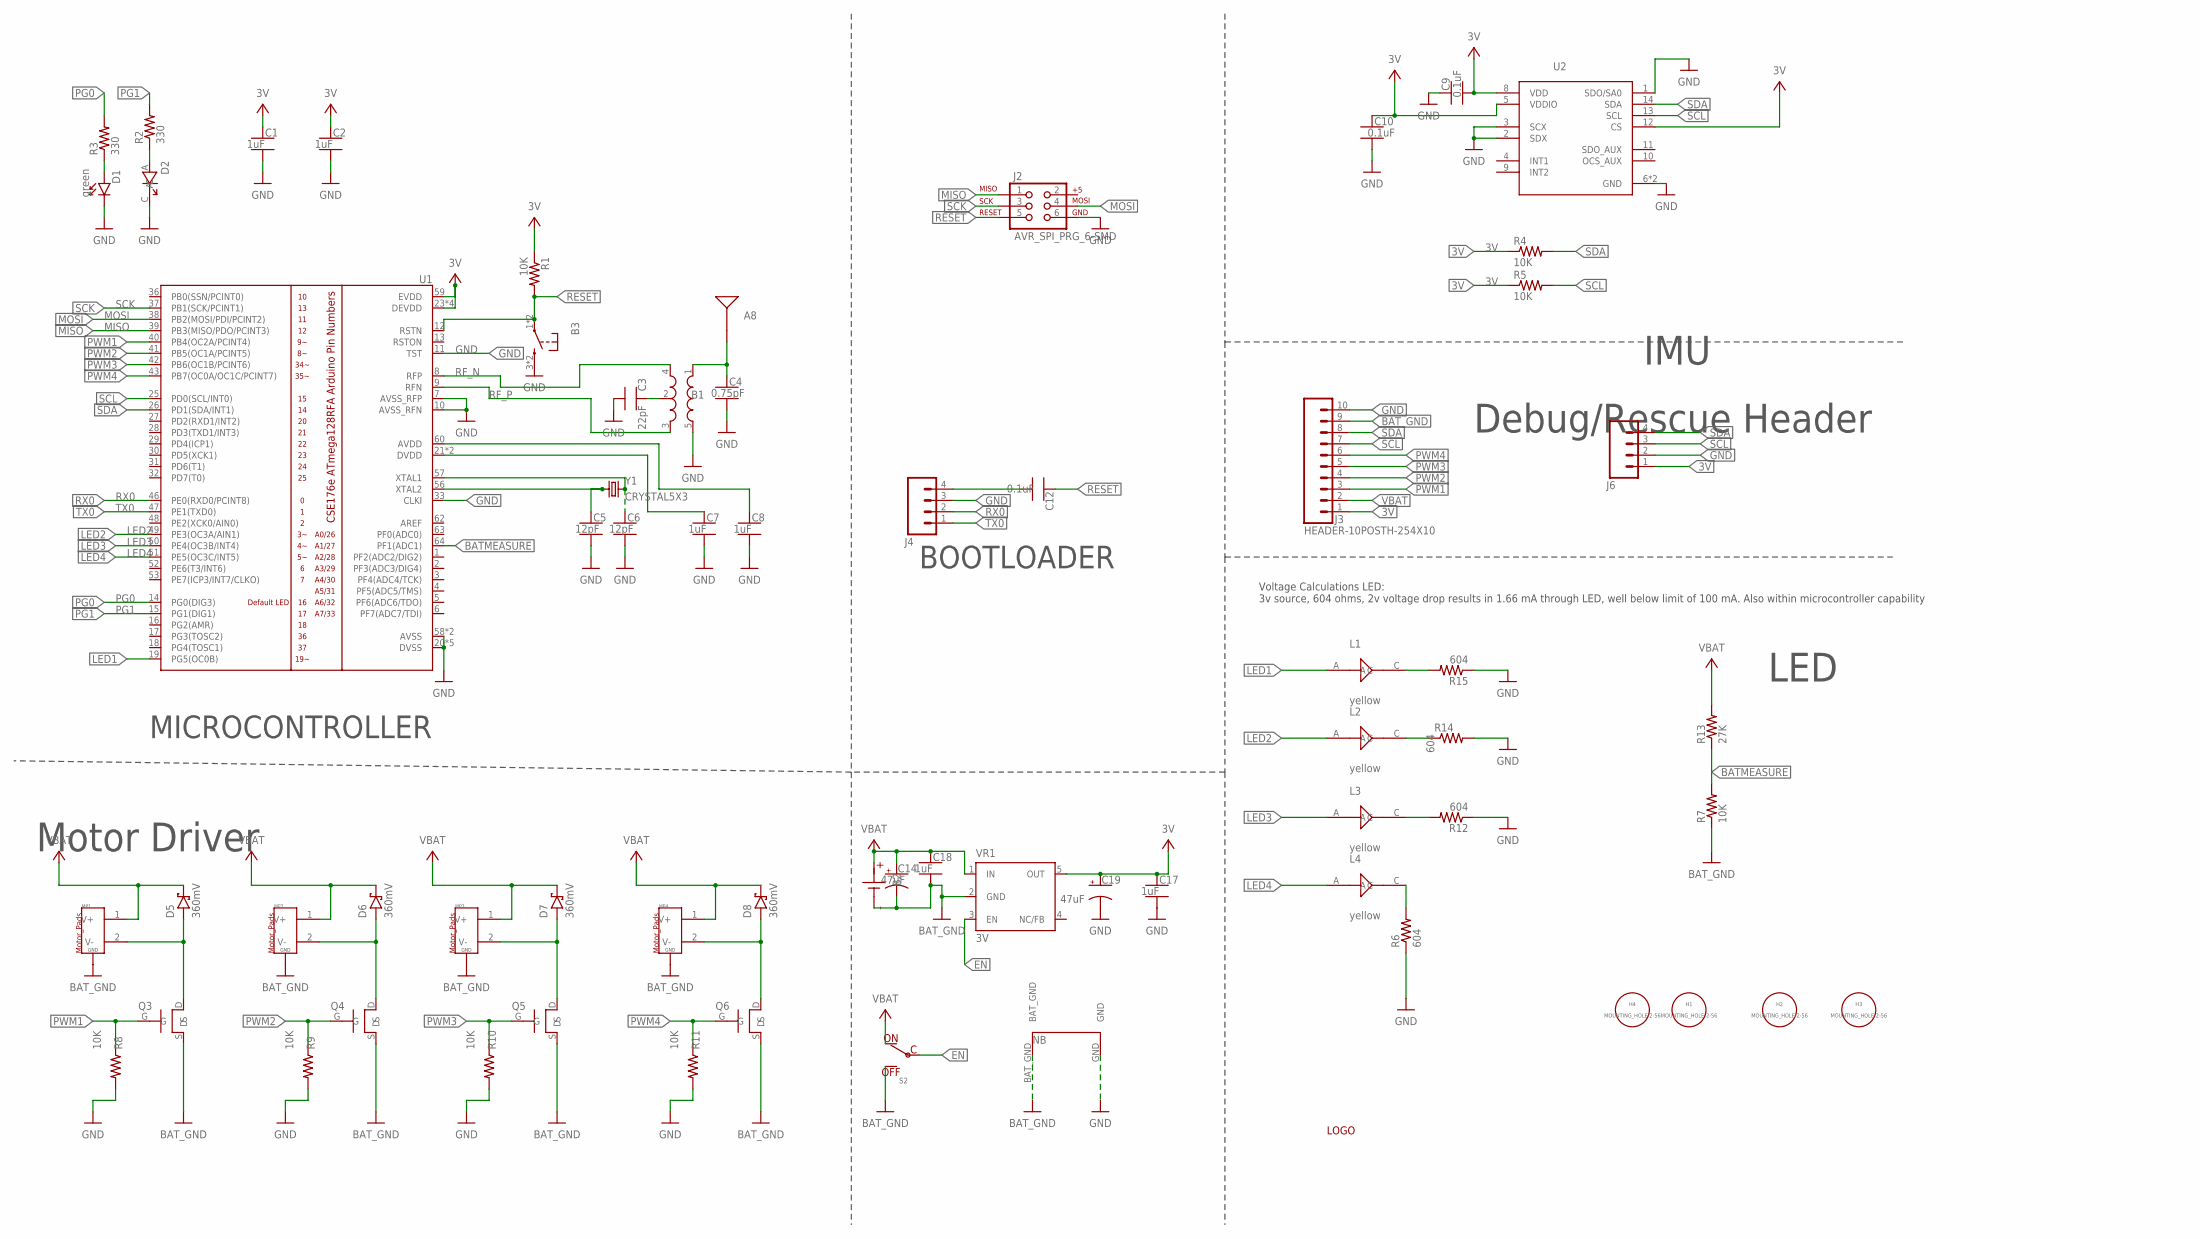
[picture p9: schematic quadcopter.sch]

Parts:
A8: ANTENNA-BOARD; ANT_PCB_2.4GHZ_NRF8001_1.6MM_1OZ
B1: BALUN0805; BALUN
B2: BATTERY-SCREW-TERMINAL; SCREW-TERMINAL-1X2-2.54MM
B3: PUSHBUTTON_SMD-VERTICAL-1; TE_FSM8JSMA_HS
C1, C2, C7, C8, C17, C18: 1uF; CAPC2012X140_HS
C3: 22pF; CAPC2012X140_HS
C4: 0.75pF; CAPC2012X140_HS
C5, C6: 12pF; CAPC2012X140_HS
C9, C10, C12: 0.1uF; CAPC2012X140_HS
C14, C19: 47uF; CAPMP3216X180
D1: green; LEDSC125X200X120-2_HS
D2: LED-RED-160-1178-1-ND; LED_160-1178-1-ND
D5, D6, D7, D8: 360mV; SODFL3516X96
H1, H2, H3, H4: MOUNTING_HOLE-2-56; 2-56-MOUNTING-HOLE-NO-METAL
J2: AVR_SPI_PRG_6-SMD; 2X3-SMD
J3: HEADER-10POSTH-254X10; HDRV10W63P254_10X1_2540X254H838_HS
J4: HEADER-4POS-0.1IN-FEMALE-SMD-BOTTOM-ENTRY; HEADER-1X4-BOTTOM-ENTRY
J6: HEADER-4POS-0.1IN-FEMALE; HDRVR4W80P254_1X4_1066X254X850B
L1, L2, L3, L4: yellow; LEDC1507X80NYELLOW
LOGO: PIDLOGO
MP1, MP2, MP3, MP4: MOTOR_PADS_GND-MOLEX-SMD; MOLEX-0532610271
NB: NETBRIDGE
Q3, Q4, Q5, Q6: MOSFET-FET-SI2302CDS-T1-E3CT-NDSI2302CDS-T1-E3CT-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; MOSFET_FET_SI2302CDS-T1-E3CT-ND
R1, R4, R5, R7, R8, R9, R10, R11: 10K; RESC2012X60_HS
R2, R3: 330; RESC2012X60_HS
R6, R12, R14, R15: 604; RESC2012X60_HS
R13: 27K; RESC2012X60_HS
S2: POWER-SWITCH-MFS201N-9-Z-SMD-EDGE; JS102011SAQN
U1: ATMEGA128RFA1; QFN-64
U2: IMU-LSM6DSOXTR-497-18367-1-ND497-18367-1-ND; LSM6DS0
VR1: 3V; SOT23-DBV
Y1: CRYSTAL5X3; CRYSTAL-SMD-5X3

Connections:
3V: C1.1, C2.1, C9.2, C10.1, C17.1, C19.1 (+), J3.1, J6.1, R1.1, R4.1, R5.1, U1.23 (DEVDD), U1.34 (DEVDD), U1.44 (DEVDD), U1.54 (DEVDD), U1.59 (EVDD), U2.5 (VDDIO), U2.8 (VDD), U2.12 (CS), VR1.5 (OUT)
BATMEASURE: R7.2, R13.1, U1.64 (PF1(ADC1))
BAT_GND: B2.1 (N), C14.2 (-), C18.2, J3.9, MP1.G1 (GND), MP1.G2 (GND), MP2.G1 (GND), MP2.G2 (GND), MP3.G1 (GND), MP3.G2 (GND), MP4.G1 (GND), MP4.G2 (GND), NB.BAT_GND, Q3.S, Q4.S, Q5.S, Q6.S, R7.1, S2.A (OFF), VR1.2 (GND)
EN: S2.C, VR1.3 (EN)
GND: B1.5 (GND), B3.3 (2), B3.4 (2), C1.2, C2.2, C3.2, C4.2, C5.2, C6.2, C7.2, C8.2, C9.1, C10.2, C17.2, C19.2 (-), D1.C, D2.C, J2.6, J3.10, J4.3, J6.2, NB.GND, R6.1, R8.2, R9.2, R10.2, R11.2, R12.1, R14.2, R15.1, U1.7 (AVSS_RFP), U1.10 (AVSS_RFN), U1.11 (TST), U1.20 (DVSS), U1.24 (DVSS), U1.33 (CLKI), U1.35 (DVSS), U1.45 (DVSS), U1.55 (DVSS), U1.58 (AVSS), U1.61 (AVSS), U2.1 (SDO/SA0), U2.2 (SDX), U2.3 (SCX), U2.6 (GND), U2.7 (GND)
LED1: L1.A, U1.19 (PG5(OC0B))
LED2: L2.A, U1.49 (PE3(OC3A/AIN1))
LED3: L3.A, U1.50 (PE4(OC3B/INT4))
LED4: L4.A, U1.51 (PE5(OC3C/INT5))
MISO: J2.1, U1.39 (PB3(MISO/PDO/PCINT3))
MOSI: J2.4, U1.38 (PB2(MOSI/PDI/PCINT2))
unnamed: D1.A, R3.1
unnamed: D2.A, R2.1
unnamed: B1.2 (GND), C3.1
unnamed: A8.FEED, B1.1 (IN), C4.1
unnamed: C8.1, U1.60 (AVDD)
unnamed: C7.1, U1.21 (DVDD), U1.22 (DVDD)
unnamed: C6.1, U1.57 (XTAL1), Y1.3 (2)
unnamed: C5.1, U1.56 (XTAL2), Y1.1
unnamed: L1.C, R15.2
unnamed: C12.2, J4.4
unnamed: L4.C, R6.2
unnamed: L2.C, R14.1
unnamed: L3.C, R12.2
unnamed: D5.2 (A), MP1.2 (V-), Q3.D
unnamed: D6.2 (A), MP2.2 (V-), Q4.D
unnamed: D7.2 (A), MP3.2 (V-), Q5.D
unnamed: D8.2 (A), MP4.2 (V-), Q6.D
PG0: R3.2, U1.14 (PG0(DIG3))
PG1: R2.2, U1.15 (PG1(DIG1))
PWM1: J3.3, Q3.G, R8.1, U1.40 (PB4(OC2A/PCINT4))
PWM2: J3.4, Q4.G, R9.1, U1.41 (PB5(OC1A/PCINT5))
PWM3: J3.5, Q5.G, R10.1, U1.42 (PB6(OC1B/PCINT6))
PWM4: J3.6, Q6.G, R11.1, U1.43 (PB7(OC0A/OC1C/PCINT7))
RESET: B3.1, B3.2 (1), C12.1, J2.5, R1.2, U1.12 (RSTN)
RF_N: B1.4 (OUT1), U1.8 (RFP)
RF_P: B1.3 (OUT2), U1.9 (RFN)
RX0: J4.2, U1.46 (PE0(RXD0/PCINT8))
SCK: J2.3, U1.37 (PB1(SCK/PCINT1))
SCL: J3.7, J6.3, R5.2, U1.25 (PD0(SCL/INT0)), U2.13 (SCL)
SDA: J3.8, J6.4, R4.2, U1.26 (PD1(SDA/INT1)), U2.14 (SDA)
TX0: J4.1, U1.47 (PE1(TXD0))
VBAT: B2.2, C14.1 (+), C18.1, D5.1 (C), D6.1 (C), D7.1 (C), D8.1 (C), J3.2, MP1.1 (V+), MP2.1 (V+), MP3.1 (V+), MP4.1 (V+), R13.2, S2.B (ON), VR1.1 (IN)

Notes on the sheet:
BOOTLOADER
MICROCONTROLLER
Voltage Calculations LED: 3v source, 604 ohms, 2v voltage drop results in 1.66 mA through LED, well below limit of 100 mA. Also within microcontroller capability
Motor Driver
LED
Debug/Rescue Header
IMU

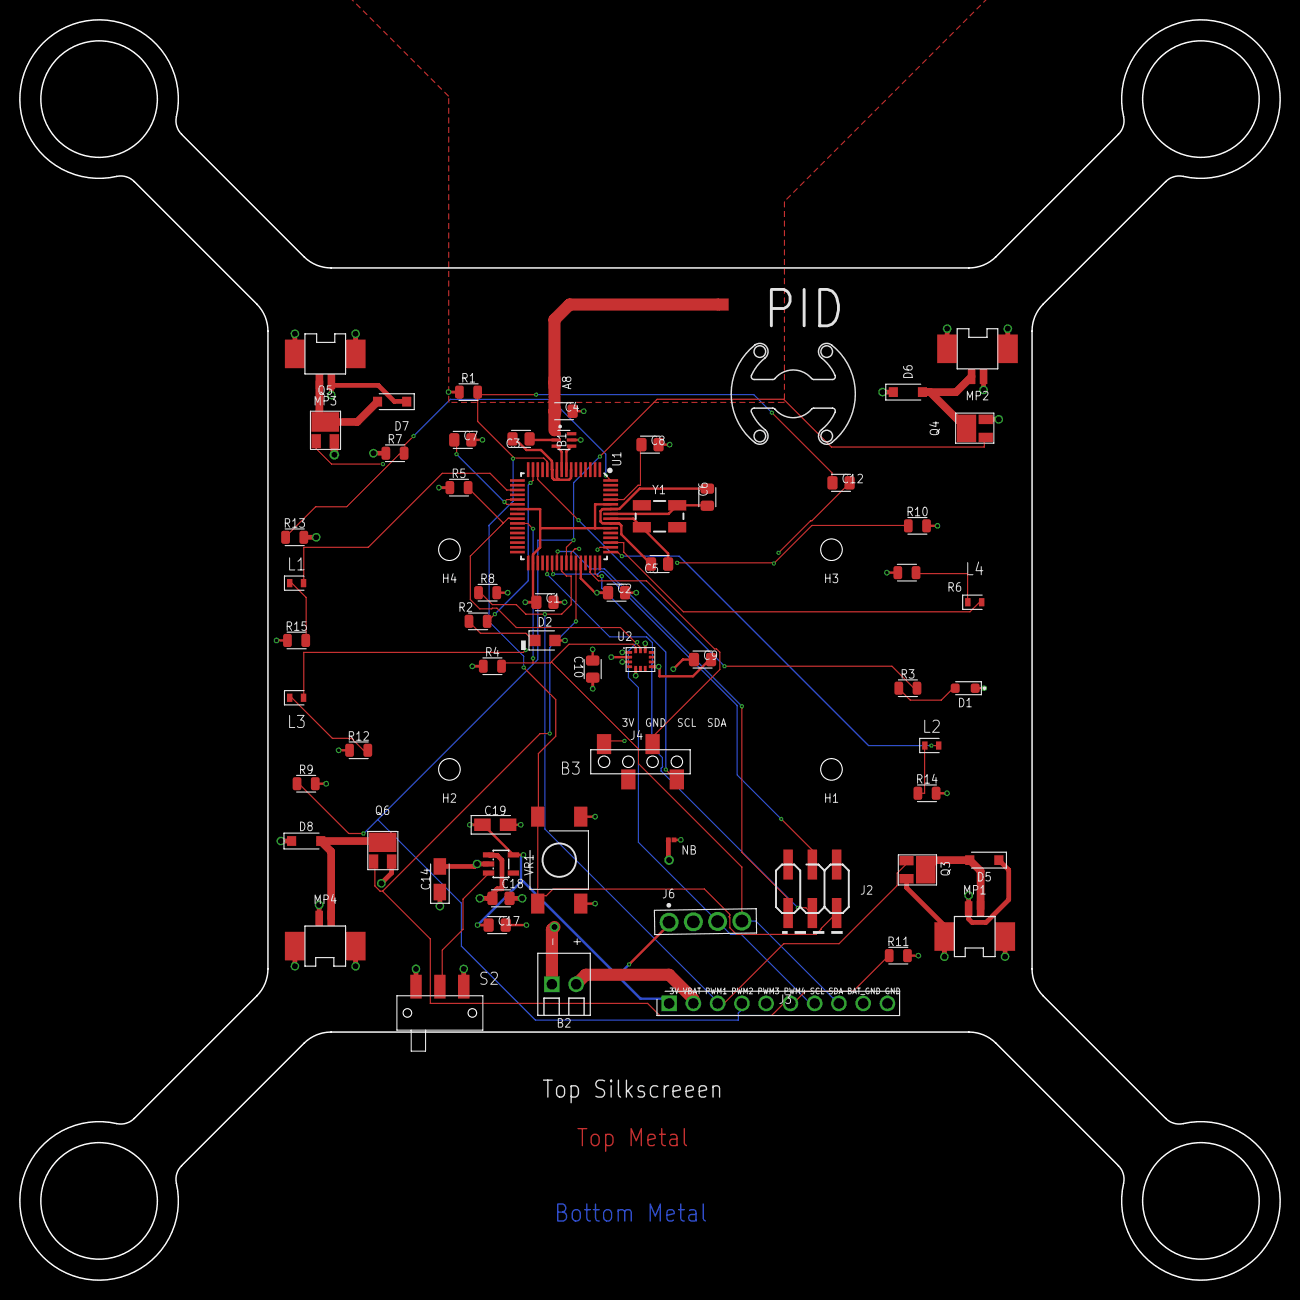
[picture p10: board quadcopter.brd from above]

Board: 4 copper layers, 132.0 x 132.0 mm, 68 parts (0 on the bottom side), 43 nets.

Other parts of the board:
U$1: LAYER_LABELS

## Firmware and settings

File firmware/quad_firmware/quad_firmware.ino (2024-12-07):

#include <radio.h>
#include <Adafruit_Simple_AHRS.h>
#include <Wire.h>
#include <Adafruit_Sensor.h>
#include <QuadClass_LSM6DSOX.h>

  uint8_t a[15] = {0};
  const int left_rear = 8;
  const int right_rear = 3;
  const int left_top = 5; 
  const int right_top = 4; 
  uint32_t start_time = 0; 
  const int magicNumber = 57;
  const int magicNumber2 = 53;

  int len = 0;

  float pitch=0.0; 
  float pitch_rate = 0.0;
  float roll=0.0;
  float yaw = 0.0;
  float target_yaw = 0.0;
  QuadClass_LSM6DSOX lsm = QuadClass_LSM6DSOX();
  Adafruit_Simple_AHRS *ahrs = NULL;
  Adafruit_Sensor *_accel = NULL;
  Adafruit_Sensor *_gyro = NULL;
  Adafruit_Sensor *_mag = NULL; 

  //complementary filter param 
  #define RAD_TO_DEG 57.295779513082320876798154814105
  float gain = 0.98; 

  double cf_pitch = 0.0;
  double cf_roll = 0.0;
  double pitch_offset = 0.0;//1.88+0.51;
  double roll_offset = 0.0; 
  double pitch_corrected = 0.0; 
  double roll_corrected = 0.0;
  double gyro_angle_yaw = 0.0;

  //pid params tuning 
  float PIDp = 0.0;
  float PIDr = 0.0;
  float PIDy = 0.0;
  float PIDy2 = 0.0;
  //int PIDoutputp = 0;
  float setpointPitchp = 0.0;
  float setpointRoll = 0.0;
  float Kpp = 0.0; //0.5  //battery on bottom: this works 0.25  0.20 0.23, 0.22
  float Kip = 0.0; //0.04, 0.05   0.01 0.002 , 0.0025
  float Kdp = 0;//0.4, 0.1  0.06 0.05, 0,032
  float Kpr = 0.0;
  float Kdr = 0.0;
  float Kir = 0.0;
  float previous_yaw_rate_error = 0.0;
  float derivative_yaw_rate = 0.0;
  double integralp = 00.00; //from 0.0
  double integralr = 00.0; //from 0.0 
  float integral_errorp = 0.0;
  float previousErrorp = 0.0;
  float max_proportional = 30.0;
  float max_derivative = 40.0;
  float max_integral = 100.0;
  
  float Kpy = 0.4; //0.5
  float Kiy = 0.0; //0.04
  float Kdy = 1.0;//0.4
  double yaw_setpoint = 0.0;  // The desired yaw rate (usually set to 0)
  float yaw_rate = 0.0;      // The current yaw rate (from the gyroscope)
  float yaw_error = 0.0;     // The difference between desired and actual yaw rate
  float previousYawError = 0.0;  // Previous yaw error (for derivative term)
  float integralYaw = 0.0;

  int16_t throttle_left_rear = 0; 
  int16_t throttle_right_rear = 0;
  int16_t throttle_left_top = 0;
  int16_t throttle_right_top = 0;

  int16_t timer = 0;
  
  int16_t throttle = 0;

  double radiotimer = 0.0;

//sensors in imu
void setupSensor()
{


 if (!lsm.begin_I2C()) {
   // Serial.println("Failed to find LSM6DSOX chip");
    while (1) {
      delay(10);
    }
  }
  _accel = lsm.getAccelerometerSensor();
  _gyro = lsm.getGyroSensor();


  ahrs = new Adafruit_Simple_AHRS(_accel, _mag, _gyro);
#
}

void setup() {
  //copied from rfecho
  rfBegin(24);  // Initialize ATmega128RFA1 radio on channel 11 (can be 11-26)
  int disarm = 1;
  disarm = 0;
  uint8_t b[6] = {0};
  b[0] = magicNumber2;
  b[1]= 57;
  b[2]=disarm;
  b[3]=0;
  b[4]=0;
  b[5] = b[0]^b[1]^b[2]^b[3]^b[4];
  rfWrite(b,6);

  //rear is where the 6 pins are sticking out
  const int SERIAL_BAUD = 19200 ;        // Baud rate for serial port 
	Serial.begin(SERIAL_BAUD);          // Start up serial

  //calling sensor meansurement func
  setupSensor();
  const int BAT_SENSE_PIN = A7; 
  pinMode(BAT_SENSE_PIN, INPUT);
  analogReference(INTERNAL);

  // global declaration of LEDs 
  const int LED1 = 16;
  const int LED2 = 17; 
  const int LED3 = 18; 
  const int LED4 = 36; 
  const int PRETTY_LEDS = 34;

  //startupRamp(); 
}

unsigned long  last = millis();
//full battery is at 885 max 
void loop() {

  int BAT_VALUE = analogRead(A7); 
  //Serial.print("Battery Voltage:"); 
  //Serial.println(BAT_VALUE);

  //checking data from imu 
  quad_data_t orientation;
  //static unsigned long  last_time = millis();
  unsigned long  now = millis();
  float dt = (now - last);
  //Serial.println(dt);
  if (ahrs->getQuadOrientation(&orientation))
  {
    /* 'orientation' should have valid .roll and .pitch fields */
    //Serial.print(now - last);
    pitch = orientation.pitch;
   //Serial.print("rawpitch:");
   //Serial.println(pitch);

    pitch_rate = orientation.pitch_rate;
    //Serial.print(" raw_pitch_rate:");
    //Serial.println(pitch_rate);
    //yaw=orientation.yaw;

    roll = orientation.roll;
    
    sensors_event_t gyro_event;
    _gyro->getEvent(&gyro_event);
    lsm.setGyroRange(LSM6DS_GYRO_RANGE_2000_DPS);
    lsm.setGyroDataRate(LSM6DS_RATE_208_HZ);

    sensors_event_t accel;
    _accel->getEvent(&accel);
    lsm.setAccelRange(LSM6DS_ACCEL_RANGE_2_G);
    lsm.setAccelDataRate(LSM6DS_RATE_208_HZ);
    lsm.setAccelCompositeFilter(LSM6DS_CompositeFilter_LPF2, LSM6DS_CompositeFilter_ODR_DIV_800);
    double gyro_raw_pitch = gyro_event.gyro.y; //.z was there initially, may need pid change
    double gyro_raw_roll = gyro_event.gyro.x;
    double gyro_raw_yaw = gyro_event.gyro.z;

  //Serial.print("\t\tAccel X: ");
  //Serial.print(accel.acceleration.x);
  //Serial.print(" \tY: ");
  //Serial.println(accel.acceleration.y);

    //Serial.print("gyro_raw_pitch:");
   // Serial.println(gyro_raw_pitch*RAD_TO_DEG);

    
    double gyro_angle_pitch = cf_pitch + (gyro_raw_pitch * RAD_TO_DEG)*dt*0.001;
    double gyro_angle_roll = cf_roll + (gyro_raw_roll * RAD_TO_DEG)*dt*0.001;
    gyro_angle_yaw = gyro_angle_yaw + (gyro_raw_yaw*RAD_TO_DEG*dt*0.001);

    cf_pitch = (gain * gyro_angle_pitch) + (1.0-gain)*pitch;
    cf_roll = (gain * gyro_angle_roll) + (1.0-gain)*roll;
    //Serial.print(" cf_pitch:");
    //Serial.println(cf_pitch);
    
    //Serial.print("cf roll:");
    //Serial.println(cf_roll);
    //Serial.print("gyro_angle_yaw:");
    //Serial.println(gyro_angle_yaw);
    if (a[13]==1){
      pitch_offset=-cf_pitch;
      roll_offset=-cf_roll;
    }

    pitch_corrected = pitch_offset + cf_pitch; 
    roll_corrected = roll_offset+cf_roll;
    //Serial.print("pitch_offset:");
    //Serial.println(pitch_offset);
    //Serial.print("roll_offset:");
    //Serial.println(roll_offset);
    //Serial.print("pitch_corrected:");
    //Serial.println(pitch_corrected);
    //Serial.print("roll_corrected:");
    //Serial.println(roll_corrected);

   //pid code here 
   setpointPitchp = ((a[4] - 127) * (0.0787401*0.5));
   setpointRoll = ((a[5]-127)*0.0787401*0.5);
   if (abs(setpointPitchp)<1){
    setpointPitchp=0;
   }
    if (abs(setpointRoll)<1){
    setpointRoll=0;
   }
   float errorPitch = setpointPitchp - pitch_corrected; 
   float errorRoll = setpointRoll - roll_corrected;
   if(Kip == 0 ||a[2]<10){ //either Ki = 0 or Speed =0, unsure how to determine speed
      integralp = 0.0; 
   }
   else{
    integralp = errorPitch * dt*0.001+integralp;

   }
      if(a[2]<10){ //either Ki = 0 or Speed =0, unsure how to determine speed
      integralr = 0.00; 
   }
   else{
    integralr = errorRoll * dt*0.001+integralr;

   }
  //float derivativep = (errorPitch - previousErrorp) / (dt*0.001);
  float derivativep = gyro_raw_pitch*RAD_TO_DEG;
  float derivativer = gyro_raw_roll*RAD_TO_DEG;
  //derivativep = constrain(derivativep, -max_derivative, max_derivative); //constrain d
  //static float last_derivative = 0.0;
  //float filtered_derivative = 0.8 * last_derivative + 0.2 * gyro_raw_pitch * RAD_TO_DEG;
  //last_derivative = filtered_derivative; //smoothening derivative term
  //float max_integral = 10;
  //integralp = constrain(integralp, -max_integral, max_integral); //constrain i
  //Serial.println(integralp);
  PIDp = (Kpp * errorPitch) + Kip * integralp - Kdp * derivativep; //changed from derivativep to filtered_derivative
  previousErrorp = errorPitch;
  PIDr= (Kpp * errorRoll) + Kip * integralr - Kdp * derivativer;
  //Serial.print("d:");
  //Serial.println(derivativep*Kdp);
  //Serial.print("p:");
 //Serial.println(errorPitch*Kpp);
  //Serial.print(" gyro_raw_yaw:");
  //Serial.println(gyro_raw_yaw);
    
    yaw_error = yaw_setpoint - gyro_angle_yaw*RAD_TO_DEG;
    //Serial.print(yaw_error);
  //Serial.println(yaw_setpoint);
    integralYaw += yaw_error * dt;
  
  float derivativeYaw = (yaw_error - previousYawError) / dt;

  float yaw_rate_error = yaw_setpoint-gyro_raw_yaw;
  previous_yaw_rate_error = yaw_rate_error;
  
  derivative_yaw_rate = (yaw_rate_error-previous_yaw_rate_error)/dt;


  PIDy = Kpy * yaw_error + Kiy * integralYaw + Kdy * derivativeYaw;
  PIDy2 = Kpy*yaw_rate_error+Kdy*derivative_yaw_rate;

  float yaw_control_derivative = gyro_raw_yaw/dt;
  previousYawError = yaw_error;
  //Serial.println(a[1]);
  if (a[1]==1){
  flying();
  //yawcontrol2();
  }
  }

  last = now;

  
  

  int len = 0;
  
  //uint8_t a[10] = {0};
  
 if (len = rfAvailable()){
  //Serial.print("Read packets:");
  //Serial.println(len);
  if(len!=15){
  rfFlush();
 }  
 else{
    rfRead(a, len);
    //Serial.println("a9");
    //Serial.println(a[9]);
    //Serial.println(len);
    if ((a[0]==magicNumber) && (a[1]==1) && (a[14]==(a[0]^a[1]^a[2]^a[3]^a[4]^a[5]^a[6]^a[7]^a[8]^a[9]^a[10]^a[11]^a[12]^a[13]))){//adding && len==4 check fails - len seems to be assigned to 130 instead... sometimes 126
      //start_time = 0; 
      analogWrite(LED1, 200);
      //analogWrite(LED2, 200);
      throttle=a[2];
      //Serial.println(a[2]);
      //int16_t a3 = a[3]; //converting to larger data type to avoid loop-around in conversion
      yaw_setpoint = (a[3]-123)*0.03 ;//conversion to deg
      if (abs(yaw_setpoint)<0.5){
        yaw_setpoint=0.0;
      }
      //Serial.println(a[3]);
      float a6=a[6];//Stop the values from getting rounded away
      float a7=a[7];
      float a8=a[8];
      float a11=a[11];
      //Serial.println(a11);
      float a12=a[12];

      Kpp=a6/100;
      Kdp=a7/100;
      Kip=a8/100;
      //Kpy=a6/100;
      //Kdy=a7/100;
      //Kiy=a8/1000;
      Kpy = a[9];

      pitch_offset=(a11-127)/10;
      roll_offset=(a12-127)/10;

      //Kdy = a[10]; 
      //Serial.print("yaw_setpoint");
      //Serial.println(yaw_setpoint);
      radiotimer=0.0;
    }
    else{
      rfFlush();
    }
   }
  //Serial.print("-90:");
  //Serial.println(-90);
  //Serial.print("90:");
  //Serial.println(90);
  }

  uint8_t b[4] = {0};
  b[0] = magicNumber2;
  b[1]= BAT_VALUE;
  //Serial.println(integralr);
  b[2]=0;
  b[3] = integralp/5;
  b[4] = integralr/5;
  //Serial.println(b[2]);
  b[5] = b[0]^b[1]^b[2]^b[3]^b[4];
  
  timer = timer+dt;
  radiotimer = radiotimer+dt;
  if (timer>50){
  rfWrite(b,6);
  timer = 0;
  }
  if (radiotimer > 1000){
  a[1]=0;
throttle=0;
PIDy=0;
PIDp=0;
analogWrite(left_rear, 0);
analogWrite(right_rear, 0);
analogWrite(left_top, 0);
analogWrite(right_top, 0);
  }
  
}

void mixing(){
//Serial.println("Throttle:");
//Serial.print(throttle);
//PIDp=constrain(PIDp,-5,5);
throttle_left_rear = throttle+PIDp;
throttle_left_top = throttle + PIDp;
throttle_right_rear = throttle - PIDp;
throttle_right_top = throttle - PIDp;
//Serial.print("PRE_PID:");
//Serial.println(PIDp);
float ratio_scale_p = 255/(throttle + PIDp);
throttle_left_rear = ratio_scale_p*constrain(throttle_left_rear, 0, 255);
throttle_right_rear = ratio_scale_p*constrain(throttle_right_rear, 0 ,255);
throttle_left_top = ratio_scale_p*constrain(throttle_left_top, 0,255);
throttle_right_top = ratio_scale_p*constrain(throttle_right_top, 0,255);
analogWrite(left_rear, throttle_left_rear);
analogWrite(right_rear, throttle_right_rear);
analogWrite(left_top, throttle_left_top);
analogWrite(right_top, throttle_right_top);

}

void startupRamp(){
    int i=0;
  for (i=0; i<50; i+=5) {
    analogWrite(left_rear, i);
    analogWrite(right_rear, i);
    analogWrite(left_top, i);
    analogWrite(right_top, i);
    delay(500);
  }
}


void yawcontrol2(){
//PIDy=constrain(PIDy2,-20,20);
throttle_left_rear = throttle+PIDy2;
throttle_left_top = throttle - PIDy2;
throttle_right_rear = throttle - PIDy2;
throttle_right_top = throttle + PIDy2;
//Serial.print("PIDyaw:");
//Serial.println(PIDy);
throttle_left_rear = constrain(throttle_left_rear, 0, 255);
throttle_right_rear = constrain(throttle_right_rear, 0 ,255);
throttle_left_top = constrain(throttle_left_top, 0,255);
throttle_right_top = constrain(throttle_right_top, 0,255);
analogWrite(left_rear, throttle_left_rear);
analogWrite(right_rear, throttle_right_rear);
analogWrite(left_top, throttle_left_top);
analogWrite(right_top, throttle_right_top);
}

void flying(){
//Serial.println("Throttle:");
//Serial.print(throttle);

//PIDp=constrain(PIDp,-40,40);
//PIDr=constrain(PIDr,-40,40);
//float ratio_scale = 255/(throttle + abs(PIDp + PIDr + PIDy2));
//PIDy2=constrain(PIDy2,-10,10);
throttle= constrain(throttle,0,255);
throttle_left_rear = throttle+PIDp-PIDr+PIDy2;
throttle_left_top = throttle + PIDp+PIDr-PIDy2;
throttle_right_rear = throttle - PIDp-PIDr-PIDy2;
throttle_right_top = throttle - PIDp+PIDr+PIDy2;
//Serial.println(PIDp);
//Serial.println(PIDr);

int big1=max(throttle_left_rear,throttle_left_top);
int big2=max(throttle_right_rear,throttle_right_top);
int biggest=max(big1,big2);
biggest=biggest-255;
if (biggest>0) {
throttle_left_rear = throttle_left_rear-biggest;
throttle_right_rear = throttle_right_rear-biggest;
throttle_left_top = throttle_left_top-biggest;
throttle_right_top = throttle_right_top-biggest;
}
//Serial.print("PRE_PID:");
//Serial.println(PIDp);
throttle_left_rear = constrain(throttle_left_rear, 0, 255);
throttle_right_rear = constrain(throttle_right_rear, 0 ,255);
throttle_left_top = constrain(throttle_left_top, 0,255);
throttle_right_top = constrain(throttle_right_top, 0,255);
analogWrite(left_rear, throttle_left_rear);
analogWrite(right_rear, throttle_right_rear);
analogWrite(left_top, throttle_left_top);
analogWrite(right_top, throttle_right_top);
//Serial.println(throttle_left_rear);
//Serial.print(throttle_right_rear);
//Serial.print(throttle_left_top);
//Serial.print(throttle_right_top);

}

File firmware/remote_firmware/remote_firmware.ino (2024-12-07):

#include <radio.h>
#include "quad_remote.h"  // Header file with pin definitions and setup
#include <serLCD.h>
#include <EEPROM.h>
//serLCD lcd; //idk why but this doesn't compile. Maybe changing it to SerLCD fixes it? Removing it doesn't seem to cause any issue.

uint8_t a[15] = {0};
//copied from the knob example
void knobs_update();
void knob_pressed(bool);
void btn1_pressed(bool);
void btn2_pressed(bool);

void btn_up_pressed(bool down);
void btn_down_pressed(bool down);
void btn_left_pressed(bool down);
void btn_right_pressed(bool down);
void btn_center_pressed(bool down);

int max_gimbal_l_vert_ad = 0;
int min_gimbal_l_vert_ad = 2;

int max_gimbal_r_vert_ad = 4;
int min_gimbal_r_vert_ad = 6;

int max_gimbal_l_hor_ad = 8;
int min_gimbal_l_hor_ad = 10;

int max_gimbal_r_hor_ad = 12;
int min_gimbal_r_hor_ad = 14;

int p_ad = 16;
int i_ad = 18;
int d_ad = 20;

float Kp = 0.99; //0.13 0.5  //battery on bottom: this works 0.25  0.20 0.23, 0.22
float Ki = 1.58; //0.15 0.02 0.04, 0.05   0.01 0.002 , 0.0025
float Kd = 0.20;//0.04 0.4, 0.1  0.06 0.05, 0,032

float Kpy=40.0;

float trimp=1.20;
float trimr=-1.40;

bool knob_down=0;
uint32_t start_time = 0; 

//data corresponding to max and min gimbal (top-bottom)

uint8_t gimbal_value_l = 0;
uint8_t gimbal_value_r = 0;
int16_t max_gimbal_l_vert = 1023;  //uint8_t only goes to 255 so I changed this data type. Also, we want a signed int - we get negative values sometimes
int16_t min_gimbal_l_vert = 0;

int16_t max_gimbal_l_hor = 0;
int16_t min_gimbal_l_hor = 0;

//added for right updown
int16_t max_gimbal_r_vert = 1023;  
int16_t min_gimbal_r_vert = 0;

int16_t max_gimbal_r_hor = 0;
int16_t min_gimbal_r_hor = 0;

const int magicNumber = 57;
const int magicNumber2 = 53;
const int SERIAL_BAUD = 19200;
const int channel = 24;

const int BAT_SENSE_PIN = A7;
const int max_bat_remote = 57;
const int min_bat_remote = 7;
const int max_bat_quad = 115; // 885; I was getting different values in testing than we recorded earlier
const int min_bat_quad = 25; // 750;
int remotebattery = 0;

int leftupdown = 0;
int rightupdown = 0;
int leftsideways = 0;
int rightsideways = 0;
int armed=0;
int len = 0;
int i = 0;

//battery voltage seems to be capped at 57 using analogReference(INTERNAL);
//7 is the lowest I've seen. But not sure if 7 means high or low voltage? seems like 7 should mean lower...
void setup() {
  Serial.begin(SERIAL_BAUD);
  pinMode(BAT_SENSE_PIN, INPUT);
  analogReference(INTERNAL);

  quad_remote_setup();

  rfBegin(channel);  //radio stuff
  rfPrint("ATmega128RFA1 Dev Board Online!\r\n");

  max_gimbal_l_vert=EEPROM.get(max_gimbal_l_vert_ad,max_gimbal_l_vert);
  min_gimbal_l_vert=EEPROM.get(min_gimbal_l_vert_ad,min_gimbal_l_vert); //I think we have to increment the EEPROM addresses by two as the gimbal values take up two bytes
  //Serial.println(max_gimbal_l_vert);

  max_gimbal_l_hor=EEPROM.get(max_gimbal_l_hor_ad,max_gimbal_l_hor);
  min_gimbal_l_hor=EEPROM.get(min_gimbal_l_hor_ad,min_gimbal_l_hor);

  //added for right updown
  max_gimbal_r_vert=EEPROM.get(max_gimbal_r_vert_ad,max_gimbal_r_vert);
  min_gimbal_r_vert=EEPROM.get(min_gimbal_r_vert_ad,min_gimbal_r_vert);

  max_gimbal_r_hor=EEPROM.get(max_gimbal_r_hor_ad,max_gimbal_r_hor);
  min_gimbal_r_hor=EEPROM.get(min_gimbal_r_hor_ad,min_gimbal_r_hor);

  knobs_update_cb = knobs_update; 
  knob1_btn_cb = knob_pressed;
  btn1_cb = btn1_pressed;
  btn_left_cb =  btn_left_pressed;
	btn_right_cb = btn_right_pressed;
	btn_center_cb =  btn_center_pressed;
  btn_down_cb = btn_down_pressed;
  //bool btn_left= btn_left_pressed;
  //testing for gimbal calibration
  /* while (millis() < 1000) {
    gimbal_value_l = analogRead(A1);
    gimbal_value_r = analogRead(A3);

    if (gimbal_value_l > max_gimbal){
      int max_gimbal_l = gimbal_value_l; 
    }

    if (gimbal_value_r > max_gimbal){
      int max_gimbal_r = gimbal_value_r; 
    }
  }
*/
}

void loop() {
  // put your main code here, to run repeatedly:
  //This was very heavily inspired by the AnalogReadSerial Example
  //involves battery and gimbal control
  int leftsideways = analogRead(A0);
  //Serial.println(leftsideways);
  int leftupdown = analogRead(A1);
  //Serial.print(leftupdown);
  int rightsideways = analogRead(A2);
  int rightupdown = analogRead(A3);
  
  int BAT_SENSE_PIN = analogRead(A7);

  //Serial.println(leftsideways);
  //Serial.println(rightsideways);
  //Serial.println(rightupdown);
  //Serial.print("Battery Voltage:");
 // Serial.println(BAT_SENSE_PIN);

  uint8_t a[15] = {0};
  a[0] = magicNumber;

  a[1]=armed;

  leftupdown = constrain(leftupdown, min_gimbal_l_vert, max_gimbal_l_vert);
  leftupdown = map(leftupdown, min_gimbal_l_vert, max_gimbal_l_vert, 0, 255);
 // Serial.println(leftupdown);

  rightupdown = constrain(rightupdown, max_gimbal_r_vert, min_gimbal_r_vert);
  rightupdown = map(rightupdown, min_gimbal_r_vert, max_gimbal_r_vert, 0,255);

  leftsideways = constrain(leftsideways, min_gimbal_l_hor, max_gimbal_l_vert);
  leftsideways = map(leftsideways, min_gimbal_l_hor, max_gimbal_l_vert, 0, 255);

  rightsideways = constrain(rightsideways, min_gimbal_r_hor, max_gimbal_r_hor);
  rightsideways = map(rightsideways, min_gimbal_r_hor, max_gimbal_r_hor, 0,255);
 // Serial.println(rightupdown);

  if (leftupdown==0 && knob_down == 1){
  update_display();
  lcd.print("Quadcopter Armed");
  armed = 1;
  }

  a[2] = leftupdown;
  a[3] = leftsideways;
  //Serial.println(a[3]);
  a[4] = rightupdown;
  //Serial.println(a[4]);
  a[5] = rightsideways;
  a[6]=Kp*100; //Convert to int
  a[7]=Kd*100;
  a[8]=Ki*100;

  a[9] = Kpy; 
  a[11] = trimp*10+127;
  a[12] = trimr*10+127;
  //Serial.println(leftupdown);

  a[14] = a[0]^a[1]^a[2]^a[3]^a[4]^a[5]^a[6]^a[7]^a[8]^a[9]^a[10]^a[11]^a[12]^a[13];




	if (is_pressed(BUTTON_UP_PIN)&&armed==0) {
		calibrate();
    armed = 0;
	}

remotebattery = map(BAT_SENSE_PIN, min_bat_remote, max_bat_remote, 0, 100);

  if (armed==1){
  update_display();
  lcd.print("Armed ");
  lcd.print("remote:");
  lcd.print(remotebattery);
  lcd.print("%");
}
else{
  update_display();
  lcd.print("Unarmed ");
  lcd.print("remote:");
  lcd.print(remotebattery);
  lcd.print("%");
}

  //rfWrite(a, 10);
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

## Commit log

2024-10-12 partial code for calibration
2024-10-13 radio control of throttle works
2024-10-14 print hi
2024-10-14 calibration for throttle only, not saved yet
2024-10-14 calibration for throttle only, now saved to EEPROM
2024-10-15 still faulty issues with data packet
    [quad_firmware.ino, remote_firmware.ino]
2024-10-15 fixed quadcopter freaking out on calibration issue
    [quad_firmware.ino, remote_firmware.ino]
2024-10-15 with right updown calibration
2024-10-15 calibration for all 4 axes
2024-10-15 added LED when armed, disarm function, stopped risk of quadcopter timing increment overflow
2024-10-15 quadcopter sends battery to remote, remote displays both batteries, battery % shown, remote disarms upon losing quadcopter connection, LED displays connection status, only issue is the remote disarms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
    [quad_firmware.ino, remote_firmware.ino]
2024-10-15 fixed typo in calibration
    [remote_firmware.ino]
2024-10-17 the interference situation is improved by reading all the packets that come in and parsing that for a valid packet. But it still fails in high-noise
    [quad_firmware.ino, remote_firmware.ino]
2024-10-17 test of schematic
    [Microcontroller_Schematic_v41.sch]
2024-10-19 check issue with code for data acq and graph
    [quad_firmware.ino]
2024-10-19 issues but tried to fix some plotting issues
    [quad_firmware.ino]
2024-10-19 no compilation issues for emu data pitch and pitch rate
    [quad_firmware.ino]
2024-10-20 added code for complementary filtering (Filtering in Software part of lab)
2024-10-20 complementary filtering in comments
2024-10-20 moving schematic for eaglint
    [quadcopter.sch]
2024-10-21 battery voltage
2024-10-21 debugging disconnect issues, without much success yet
    [quad_firmware.ino, remote_firmware.ino]
2024-10-21 fixing many eaglint errors, mostly disconnected nets
    [quadcopter.sch]
2024-10-21 led updates and minor fixes, like reconnecting bad labels
2024-10-21 can now successfully filter interference from other channels, but not on the same channel yet. At least no more crashing, even with interference on the same channel
    [quad_firmware.ino, remote_firmware.ino]
2024-10-21 see what new issues we have
    [quadcopter.sch]
2024-10-21 a few less errors
    [quadcopter.sch]
2024-10-21 fixing voltage regulator/switch
    [quadcopter.sch]
2024-10-22 please work
    [quadcopter.sch]
2024-10-22 fixed issues with sensor outputs
    [quad_firmware.ino]
2024-10-22 lets see what needs to be fixed
    [quadcopter.sch]
2024-10-22 fixed power supply stuff, a lot of broken led nets, still havent found N...
    [quadcopter.sch]
2024-10-22 fixing library issues mostly, also a netbrige error, stil cant find N
    [quadcopter.sch]
2024-10-22 fixing LED values, more library dependencies
    [quadcopter.sch]
2024-10-22 swap out battery
    [quadcopter.sch]
2024-10-22 fix missing net in schematic
    [quadcopter.sch]
2024-10-24 fixing quadcopter schematic
    [quadcopter.sch]
2024-10-24 fixing imu rescue header
    [quadcopter.sch]
2024-10-29 check, lots of work from both of us
    [quadcopter.brd]
2024-10-29 update schematic
    [quadcopter.sch]
2024-10-31 fixing many issues from quick check
    [quadcopter.brd, quadcopter.sch]
2024-10-31 ready for full check, fixed last few trivial issues
    [quadcopter.brd]
2024-11-01 fixed a bunch of routing issues/vias, added logo
    [quadcopter.brd, quadcopter.sch]
2024-11-01 fixed high-current net issues
    [quadcopter.brd, quadcopter.sch]
2024-11-01 removed invisible net
    [quadcopter.sch]
2024-11-02 preliminary PID code. Not guaranteed to work as intended
2024-11-02 i really hope this passes
    [quadcopter.brd, quadcopter.sch]
2024-11-02 i really hope this one passes
    [quadcopter.brd, quadcopter.sch]
2024-11-04 pid tweaks+mixing redo+stopped using delay to delay and instead use a millis() count so everything else runs faster
2024-11-05 added pid debugs but not working
    [quad_firmware.ino]
2024-11-05 final manufacturing (hopefully) :)
    [quadcopter.brd, quadcopter.sch]
2024-11-05 :) :D ;)
    [quadcopter.brd]
2024-11-05 final board? :)
    [quadcopter.brd, quadcopter.sch]
2024-11-05 pid maybe works
2024-11-07 added some raw code for yaw
2024-11-07 adding buttons
2024-11-11 finally hovers reasonably well with pitch
2024-11-11 works for pitch control. Fixed radio overflow issue.
    [quad_firmware.ino, remote_firmware.ino]
2024-11-12 yaw kind of works
2024-11-12 works for pitch+yaw seperately
2024-11-12 ceiling on pid helps with instability
2024-11-14 knob and buttons read now but not implemented. very very tired and stressed. long week.
2024-11-14 we're screwed
2024-11-15 bill of materials with parts checked off
2024-11-17 added rad-to-deg for derivatived, flipped sign so it does what we want, fixed data loss issue when transmitting due to int to float conversion
    [quad_firmware.ino, remote_firmware.ino]
2024-11-17 added filter to smoothen d, constrains to d,i
2024-11-19 kind of semi works for both pitch+yaw
2024-11-21 added yaw button
2024-11-21 working yaw
2024-11-23 now you can push the bottom button to level. Also the first attempt at a flying function was made. Right now it is just a flip over onto the floor function
    [quad_firmware.ino, remote_firmware.ino]
2024-11-29 new mixing algorithm ensures that pid values are fully applied even at 255 throttle
2024-12-01 fix for mixing algorithm
    [quad_firmware.ino]
2024-12-03 fixed pitch+yaw, bizzarely high i change to make it work tonight...
    [quad_firmware.ino, remote_firmware.ino]
